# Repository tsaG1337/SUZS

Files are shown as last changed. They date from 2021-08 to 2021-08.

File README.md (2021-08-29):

# SÜZS
The **S**pannungs**Ü**berwachungs**Z**entral**S**teuerungsplatine to control your 3D Printer.

The SUZS gives you control over your 3D Printer instantly without the need to power your Raspberry or your MCU, either via pushbuttons or over network.
Need to switch on the lights to watch your print via webcam? No problem!
This is currently a WIP. Although first prototypes are up and running, there might be some things that will be changed/added in the future.

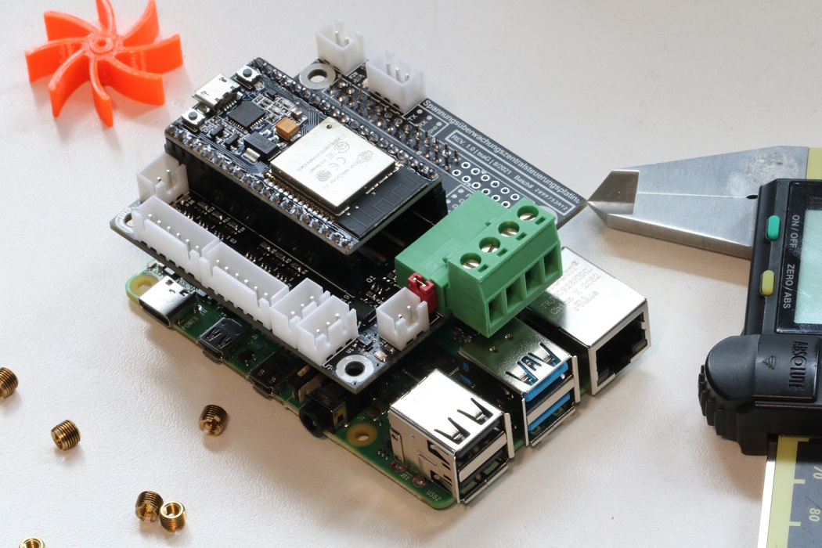
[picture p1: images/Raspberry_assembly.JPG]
Raspberry Assembly


## Main Features:

* Implementation into Home-Assist
  * Control the Power of your printer over the net or with your favourite voice assistant (Siri, Alexa etc.)
* Fundamental 3D Printer Control.
  * Support for a Print Chamber heater and Fan combination.
  * Safely Power your Raspberry Pi with the touch of a button. Regardless of whether its the physical button on your printer itself, or over the WEB-IDE.
  * Once you are done, let the SUZS send the Shutdown command to safely shut down your Pi and cut the power (hey, you are doing something good for the environment!).
  * Raspberry Input Voltage Check.
  * Raspberry Pi UART to Control Board Header (no need to use the bulky USB cable anymore)
* W2812B / Neopixel Levelshifter to set the special mood for you and your printer including WLED (The ESPHome WLED implementation is currently WIP)..
* LED control can be bridged from Klipper control to match the color theme your printing stats (TBD)
* Control for external/electronics compartment Fan / Pump (including Power PWM or PWM Signal). Normally supplied by 5V, optionally up to 25V.
* Air Temp Sensor
* Interface for 2 RGB Buttons (Mainly used for Power and Lighting)
* Emergency Off Button
* Wattmeter input: See how much power you have drawn during printing by connecting an external power counter.

## Hardware

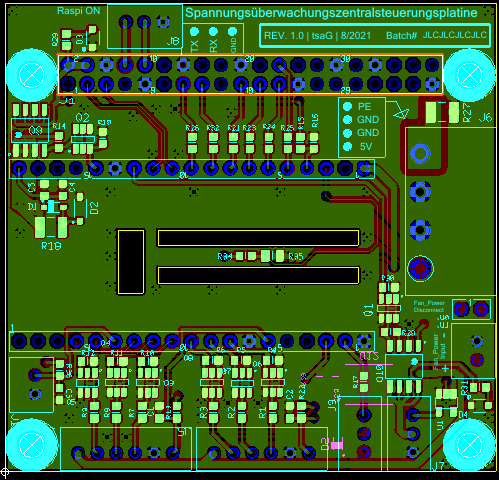
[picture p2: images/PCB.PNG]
SUZS PCB


The SÜZS is designed as a HAT/Piggyboard for a Raspberry Pi. The controller used is an ESP32 NodeMCU. 
There are several version of this Board on the market, one has to check the Pinout to find a matching one.
This Board has 19x2 Pins to connect to the SÜZS.

<p align="center">
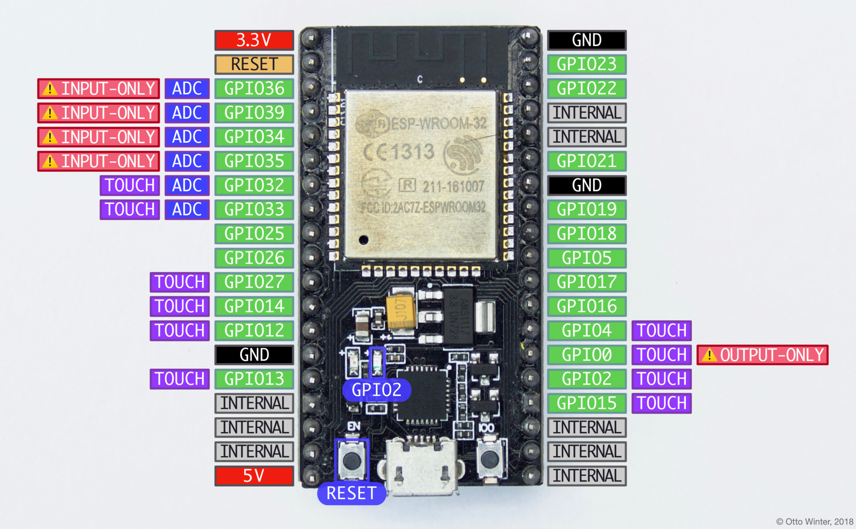
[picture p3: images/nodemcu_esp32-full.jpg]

</p>

## Software

The Firmware will be based on the ESPHome Project including some realtime GPIO checks for Power Monitoring and Raspberry Status control.
You are able to Monitor the basics via Home-Assist and also hit the E-Stop button from the warmth of your chair.

<p align="center">
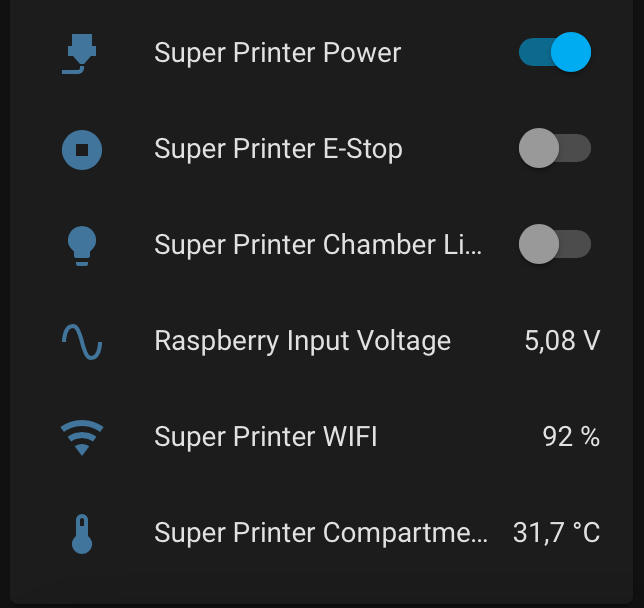
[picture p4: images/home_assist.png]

</p>

Pick your favourite Color in the web interface to set the theme for your printer. 
The color picked for the printing Chamber lighting, sets the theme for all RGB LEDs connected. 

<p align="center">
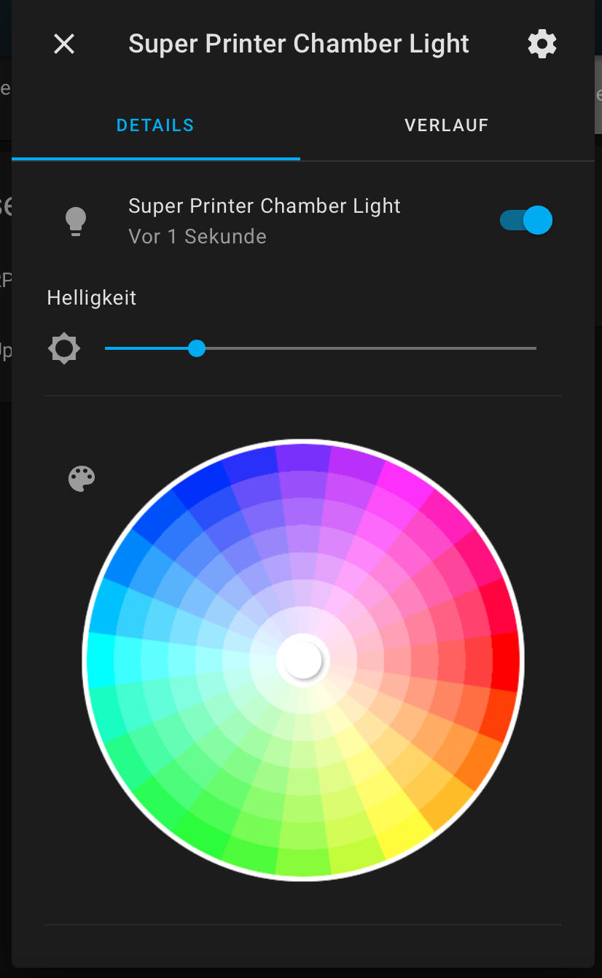
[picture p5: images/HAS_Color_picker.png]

</p>

## Changelog:

### Hardware Rev 0.2

- Added 2 NTC Sensors (Chamber heater output and Chamber heater)
- Discrete RGB Outputs (Power and Light Button) are now designed for common Cathode LEDs
- Added Filtering capacitors to the 5V Rail (the RGB Strip created some noise that lead to a reboot of the ESP)
- Added Wattmeter Pulse input.
- Added Protection diode for AC mains Relais (actually not needed as it is controlled on the high side, but you never know...)
- ~~removed external Pullups for the Switches and enabled the ESP internal ones.~~
- removed the RGB connection between RPi and ESP for the NTC and Wattmeter (RGB shall be handled via the I2C connection lateron)

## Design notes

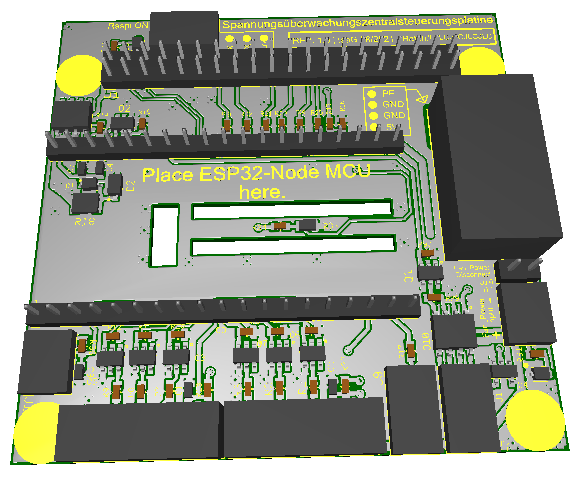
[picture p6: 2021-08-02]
images/PCB-3D.PNG

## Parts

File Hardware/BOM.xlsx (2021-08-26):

Quantity | Description | RefDes | Package | Type | Manufacturer | Manufacturer Part No.
1 | HEADERS_TEST, HDR2X20 | J1 | Generic\HDR2X20
7 | RESISTOR, 1kΩ | R1, R15, R16, R17, R21, R26, R32 | IPC-7351\Chip-R0603
1 | Def, MC74VHC1G125DBVT1G | U1 | Ultiboard\SC-74A-5
3 | CAPACITOR, 10nF | C1, C2, C3 | IPC-7351\Chip-C0603
1 | ZENER, BZT52H-C5V1 | D2 | NXP Semiconductors\SOD-123-2(SOD123F) |  | NXP Semiconductors
1 | RESISTOR, 1MΩ | R27 | IPC-7351\Chip-R1210
1 | Def, 1757268 | J6 | Ultiboard\1757268
1 | RESISTOR, 2Ω | R18 | IPC-7351\Chip-R1210
20 | RESISTOR, 4k7Ω | R9, R12, R14, R19, R25, R29, R33, R37, R40, R43, R44, R46, R47, R48, R49, R50, R51, R52, R53, R54 | IPC-7351\Chip-R0603
2 | Def, FDS6675BZ | Q9, Q10 | IPC-7351\SO-8
2 | Def, PMN30UNX | Q1, Q2 | ON Semiconductor\TSOP-6-6(CASE 318G-02U)
5 | RESISTOR, 10kΩ | R23, R24, R30, R34, R39 | IPC-7351\Chip-R0603
2 | Def, LED0603 | D3, D4 | Ultiboard\SOD2514X100
4 | RESISTOR, 2kΩ | R2, R3, R28, R31 | IPC-7351\Chip-R0603
3 | HEADERS_TEST, HDR1X3 | J7, J8, J9 | Ultiboard\B3B-XH-A
1 | HEADERS_TEST, HDR1X2 | J10 | Generic\HDR1X2
3 | RESISTOR, 100Ω | R20, R36, R38 | IPC-7351\Chip-R0603
2 | HEADERS_TEST, HDR1X19 | J3, J4 | Generic\HDR1X19
1 | POWER_MOS_N, BSC009NE2LS | Q12 | Infineon\SuperSO8(PG-TDSON-8) |  | Infineon
6 | HEADERS_TEST, HDR1X2 | J11, J12, J13, J14, J15, J16 | Ultiboard\B2B-XH-A
3 | SCHOTTKY_DIODE, BAT60A | D1, D5, D6 | Infineon\SOD-323-2(SOD323) |  | Infineon
1 | RESISTOR, Rt | R35 | IPC-7351\Chip-R0805
3 | RESISTOR, 10Ω | R41, R42, R45 | IPC-7351\Chip-R0603
2 | HEADERS_TEST, HDR1X5 | J2, J5 | Ultiboard\B5B-XH-A
6 | Def, DMC1028UVT-7 | U2, U3, U4, U5, U6, U8 | IPC-7351\TSOT23-6
2 | CAPACITOR, 100nF | C4, C6 | IPC-7351\Chip-C0603
2 | CAPACITOR, 4.7µF | C5, C7 | IPC-7351\Chip-C0603

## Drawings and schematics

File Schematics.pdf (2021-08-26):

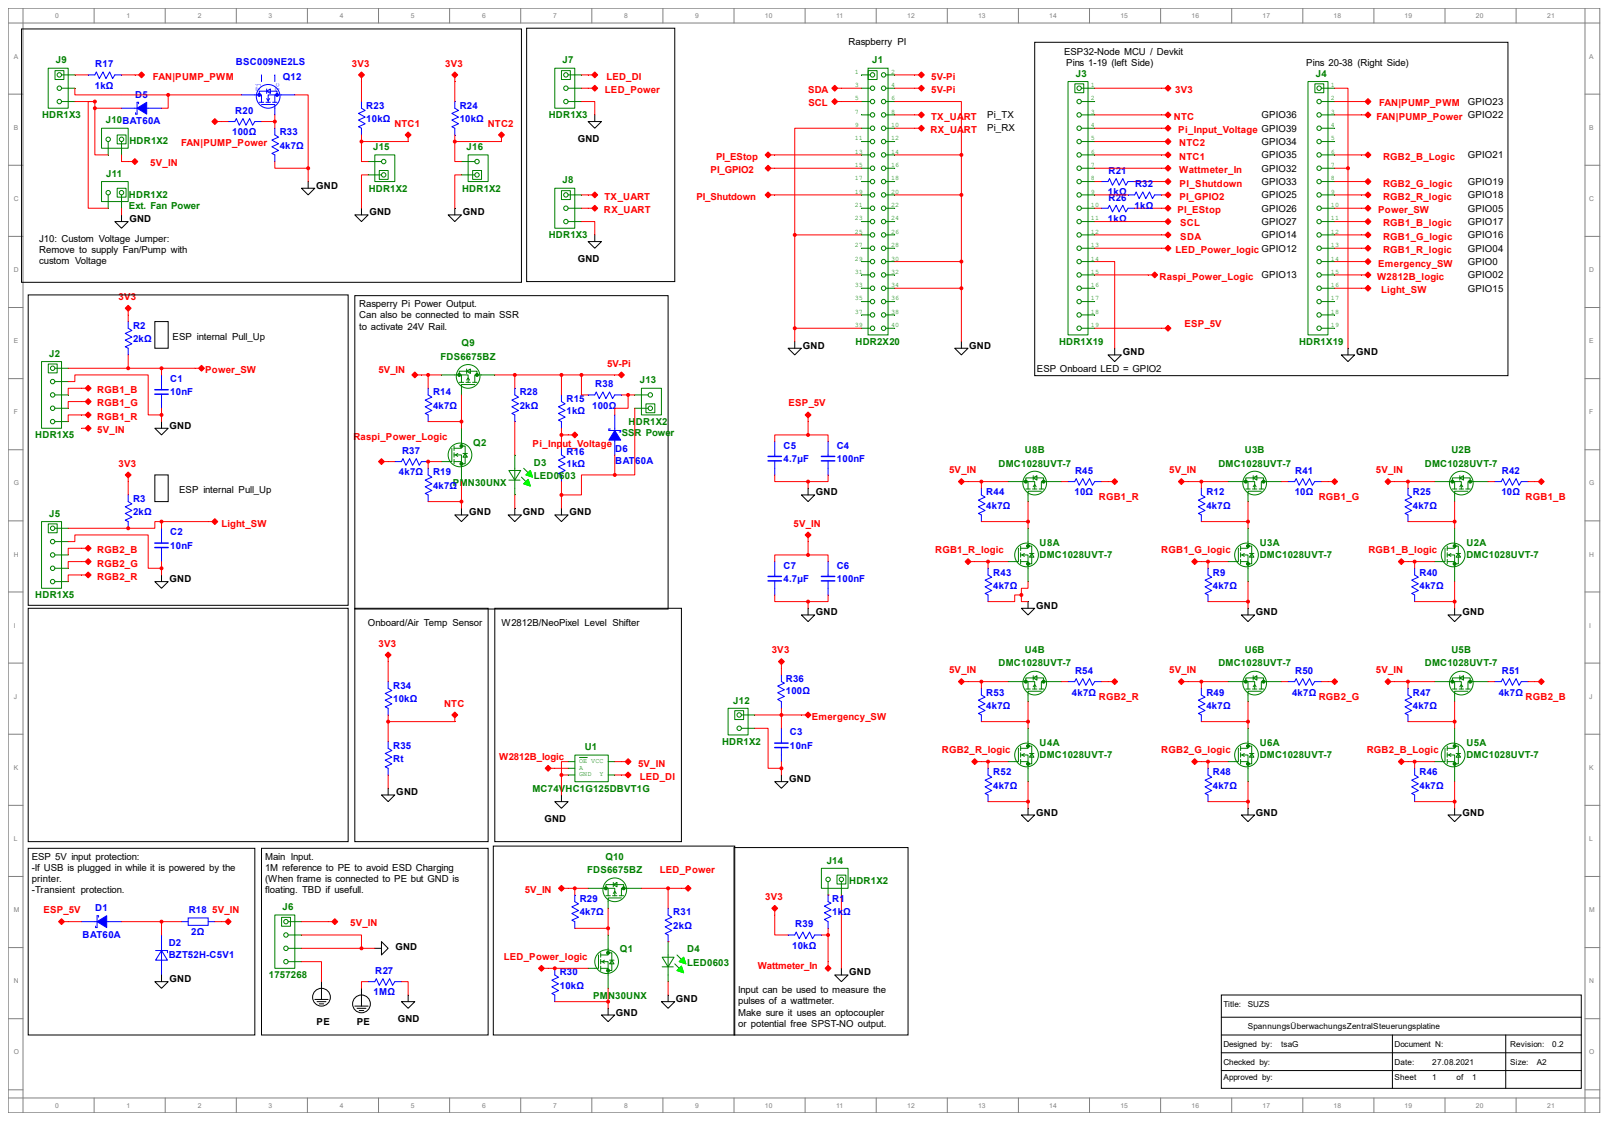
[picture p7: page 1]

J10: Custom Voltage Jumper:
Remove to supply Fan/Pump with
custom Voltage

Rasperry Pi Power Output.
Can also be connected to main SSR
to activate 24V Rail.

Onboard/Air Temp Sensor

ESP 5V input protection:
-If USB is plugged in while it is powered by the
printer.
-Transient protection.
ESP_5V

Main Input.
1M reference to PE to avoid ESD Charging
(When frame is connected to PE but GND is
floating. TBD if usefull.

Input can be used to measure the
pulses of a wattmeter.
Make sure it uses an optocoupler
or potential free SPST-NO output.

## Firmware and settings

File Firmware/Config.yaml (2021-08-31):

#/ User configuration Options /#
substitutions:

  upper_devicename: "Super Printer"
  Wifi_SSID: "SSID"
  Wifi_Password: "Password"

  #Pick your color theme. Numbers in percentages (You can use a HSL Color picker)
  redColor_val:  "1.0"
  greenColor_val: "0.4"
  blueColor_val: "0.0"
  LED_Chipset: WS2812B                      #Type of LED Strip
  led_count: "17"                           #number of LEDs connected to the WS218B Port

# Enable logging
logger:
  level: VERBOSE

esphome:
  name: suzs
  platform: ESP32
  board: nodemcu-32s
  on_boot:
    priority: -600
    then:
      - light.turn_off: powerButton_LED # Turn off the LEDS on boot
      - light.turn_off: LightButton_LED # Turn off the LEDS on boot
      - light.turn_off: chamber_light   # Turn off the LEDS on boot
      - switch.turn_off: raspi_power    # Disable raspi power on boot
      - switch.turn_off: Emergency_SW   # reset E-Stop on boot

# Enable Home Assistant API
api:

ota:
  password: "8b6f86898cf5b2142759ba8af93b0718"

wifi:
  ssid: ${Wifi_SSID}
  password: ${Wifi_Password}

  # Enable fallback hotspot (captive portal) in case wifi connection fails
  ap:
    ssid: ${upper_devicename} Fallback Hotspot
    password: "ZentralSteuerungsplatine"

captive_portal:

globals:
   - id: redColor_var
     type: float
     restore_value: no
     initial_value: ${redColor_val}

   - id: greenColor_var
     type: float
     restore_value: no
     initial_value: ${greenColor_val}    

   - id: blueColor_var
     type: float
     restore_value: no
     initial_value: ${blueColor_val}  

output:

#//Left Side of the ESP //#

#NTC (GPIO36)             ->  See Sensors
#Input Voltage (GPIO39)   -> See Sensors
#PI_R (GPIO34)            -> Not used yet
#PI_G (GPIO35)            -> Not used yet
#PI_B (GPIO32)            -> Not used yet

  - platform: gpio
    id: Pi_Shutdown_Pin
    pin: GPIO33    

  - platform: gpio
    id: Pi_eStop_pin
    pin: GPIO26   

#SCL (GPIO27)             -> Not used yet
#SDA (GPIO14)             -> Not used yet

 # - platform: gpio
 #   id: LED_Power_Pin
 #   pin: GPIO12

  - platform: gpio
    id: Raspi_Power_Pin
    pin: GPIO13        

#// Right side of the ESP //#

#FAN|Pump_PWM (GPIO23)    -> See PWM (LEDC)

  - platform: gpio
    id: Fan_Pump_Pin
    pin: GPIO22   

#Power_SW (GPIO21)        -> See Binary Sensor

  - platform: ledc
    id: RGB2_PIN_B
    pin: GPIO019

  - platform: ledc
    id: RGB2_PIN_G
    pin: GPIO018

  - platform: ledc
    id: RGB2_PIN_R
    pin: GPIO05
    
  - platform: ledc
    id: RGB1_PIN_B
    pin: GPIO017

  - platform: ledc
    id: RGB1_PIN_G
    pin: GPIO016

  - platform: ledc
    id: RGB1_PIN_R
    pin: GPIO04

    

#Emergeny_SW (GPIO0)    -> See Binary Sensor
#WS2812B_Pin (GPIO02)   -> See LED
#Light_SW (GPI15)       -> See Binary Sensor      

# Example configuration entry
power_supply:
  - id: LED_power_supply
    pin: GPIO12

binary_sensor:

  - platform: gpio
    pin:
      number: GPIO25
    id: Pi_PowerStatus

  - platform: gpio #Power Button
    pin:
      number: GPIO21
      inverted: true
    id: powerButton
    on_click:
      - min_length: 100ms
        max_length: 500ms
        then:
          - logger.log: "Short press -> Toggle Power"
          - switch.toggle: pi_power_request
          - script.execute: power_handler

      - min_length: 2000ms
        then:
          - logger.log: "Long Press -> Force off"
          - script.stop: power_handler
          - switch.turn_off: raspi_power
          - light.turn_on:
                  id: powerButton_LED
                  effect: "Fast Pulse"
                  red: ${redColor_val}
                  green: ${greenColor_val}
                  blue: ${blueColor_val}  
          - delay: 3s
          - light.turn_off: powerButton_LED             

  - platform: gpio #Light Button
    pin:
      number: GPIO15
      inverted: true
    id: lightButton
    on_click:
      - min_length: 100ms
        max_length: 500ms
        then:
          - if:
              condition: 
                - light.is_on: chamber_light
              then:
                - light.turn_off: chamber_light
                - light.turn_off: LightButton_LED
              else:
                - light.turn_on: chamber_light
                - light.turn_on: LightButton_LED
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

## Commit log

2021-08-02 Initial Beta release
    [Spannungsueberwachungszentralsteuerungsplatine - Board Outline.gbr, Spannungsueberwachungszentralsteuerungsplatine - Copper Bottom.gbr, Spannungsueberwachungsz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]
2021-08-02 Updated Gerber (Silkscreen)
    [Spannungsueberwachungszentralsteuerungsplatine - Copper Bottom.gbr, Spannungsueberwachungszentralsteuerungsplatine - Drill Symbols-Copper Top-Copper Bottom.gbr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]
2021-08-26 Move to Rev. 0.2
    Tidied up, added more information and moved up to Rev. 0.2 after the first Prototypes have been tested and Feedback implemented.
    [BOM.xlsx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]
